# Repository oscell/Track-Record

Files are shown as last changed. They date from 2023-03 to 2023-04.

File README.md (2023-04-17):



## Team

| Name | Responsibility | GUID |
|---|---|---|
| Oscar Meunier | Network and Design engineer | 2391076M |
| Sai Vamsi Karnam | Development and Integration engineer | 2805927K |
| Tara Duggan | Electronics and Design engineer | 2363956D |
| Rohith Kambampati | Backend developer and programmer | 2782679K |

Track-Record is a face tracking system built on the Raspberry Pi 3B platform, using a Pi Camera Module and servo motors for real-time face detection and tracking. A GUI is also implemented which communicates via a server sending commands to the Raspberry Pi.

The full documentation can be found [here](https://tduggan63.github.io/Track-Record/index.html).

Find us on [Twitter](https://twitter.com/TrackrecordTeam) and [Instagram](https://www.instagram.com/_u/tracknrecordteam) to stay up to date with any of the latest developements or email us at tracknrecordteam@gmail.com to get in touch.

## Hardware

The following electronic components were used to build the project:

- [Raspberry Pi 3B](https://www.raspberrypi.com/products/raspberry-pi-3-model-b/)

- [SD Card] - One with a memory capacity of 16 gigs or more.
- [Pi Camera module 2](https://www.raspberrypi.com/products/camera-module-v2/)
- [SG92R Servo](https://www.towerpro.com.tw/product/sg92r-7/)

## Software Dependencies

The following libraries were used throughout the project:

- [CMake](https://cmake.org/download/)
- [OpenCV](https://opencv.org/releases/)
- [BCM2835](https://www.airspayce.com/mikem/bcm2835/index.html)
- [QT5](https://wiki.qt.io/Qt_for_Beginners)

## Installation and Usage

This project aims to build a standalone plug and play type product.
Clip the camera of your choice to the platform, switch the power on and watch it track you.
But wait there's more, you can build it on your own. Follow the instructions ahead.

## Instructions

- Step 1: Setting up the hardware
  - [Install the OS](https://www.raspberrypi.com/documentation/computers/getting-started.html) and set up a display.*
  - [Connect the Pi camera](https://www.raspberrypi.com/documentation/computers/compute-module.html#attaching-a-raspberry-pi-camera-module)
  - Connect the motors using the PinOut diagram: Pan at Gpio 18, Tilt at Gpio 17
  - 3D print the models -- Check the Schematics and Solidworks directories or build your own model

- Step 2: Software
  - Make sure to have the latest update for the GCC/G++ compiler on your Raspberry Pi OS.
  - [Setup cmake](https://cmake.org/download/) on your Raspberry Pi.
  - Clone the repo, the libraries used are included with the git package.
  
  ```git
  git clone https://github.com/oscell/Track-Record.git
  ```
  
  - Unpack the lib_package archive to /usr/include

  ```bash
  sudo tar -xf lib_package.tar.gz -C /usr/include
  ```
  
  - Create an executable in the `main/build` directory
    - Open a terminal and navigate to the main directory
    - Run the following commands to create the executable "tracknrecord"
  
    ```bash
    mkdir -p build && cd build
    cmake ..
    make
    ```

    - You should now see two executables named "tracknrecord" and "server" in the directory
  
  - Set executable permission to run on startup
    - Open a terminal and run the following commands
  
    ```bash
    mkdir /home/pi/.config/autostart
    nano /home/pi/.config/autostart/track.desktop
    ```

    - Copy or type the following text into the "track.desktop" file.
    - Replace the "directory" with the location of the executable named 'server.cpp' located in the main folder. (eg. home/pi/...)

    ```bash
    [Desktop Entry]
    Type=Application
    Name=Track
    Exec="directory"
    ```

    - Save the file using: Ctrl+X -> Y
  
- Step 3:
  - Setup the GUI* as shown in section 2 of the footnotes.

- Step 4:
  - Reboot the Pi from the terminal and it is ready to go.

    ```bash
    sudo reboot
    ```

  - The Pi should now be listening for commands.

  - Ensure the Pi and your personal machine are on the same network.

  - Open the GUI on your personal machine and click "start tracking".

  - To view the video feed, click the video feed button.

-----------------------------------------------------------------------------------------------------------------------------------------------------------------------

## *Footnotes  
  
### Section 1: Additonal information

- [Raspberry Pi PinOut diagram](https://www.raspberrypi.com/documentation/computers/raspberry-pi.html)
- SG92r wiring: Red for Power, Brown for Ground, and Yellow/Orange for Data.
- Set up [Raspberry Pi in headless mode](https://www.realvnc.com/en/blog/how-to-setup-vnc-connect-raspberry-pi/) without a display and other hardware.

### Section 2: GUI

This section should be built locally (not on the raspberry PI). It will be used to comunicate with the PI to send commands.

#### Dependencies

As previously with the raspi install [cmake](https://cmake.org/download/) on your machine. The next step is to install [Qt5](https://www.qt.io/download) although this can be done simply on linux using the command:

```bash
sudo apt-get install qt5-default
```

To find the path of your Qt5 installation, set up the C++, cmake, and QT5 on your personal machine and run the following command in the terminal:

```bash
find / -iname Qt5Config.cmake 2>/dev/null
```

Once you have the path, you can update the `/local/CMakeLists.txt` file with the correct Qt5_DIR.

```cmake
set(Qt5_DIR "/path/to/Qt5/lib/cmake/Qt5")
```

The comunication with the raspberry pi is done through a server. To find the IP adress of the raspery pi run in the raspberry pi terminal:

```bash
hostname -I
```

In `/local/src/GUI/main.cpp` change:

```c++
QString serverAddress = "127.0.0.1";
```

to

```c++
QString serverAddress = "<raspberry_pi_ip>"
```

### Build

```bash
cd local/
mkdir -p build && cd build
cmake ..
make
```

### Usage

### On the Raspi

Before being able to run send command the server must be initialised on the raspi.

```bash
cd main/build/
./server 
```

### On your local machine

Run the GUI.

```bash
 cd local/build/
./GUI1_0
```

It is comprised of a section for vieo feed input and 2 buttons.

### Tracking button

This sends a signal to the client which toggles the tracknrecord executable depending on the state it is currently in.

### Video feed

This toggles the user webcam to show how face detection and tracking works.
The GUI should look like this:

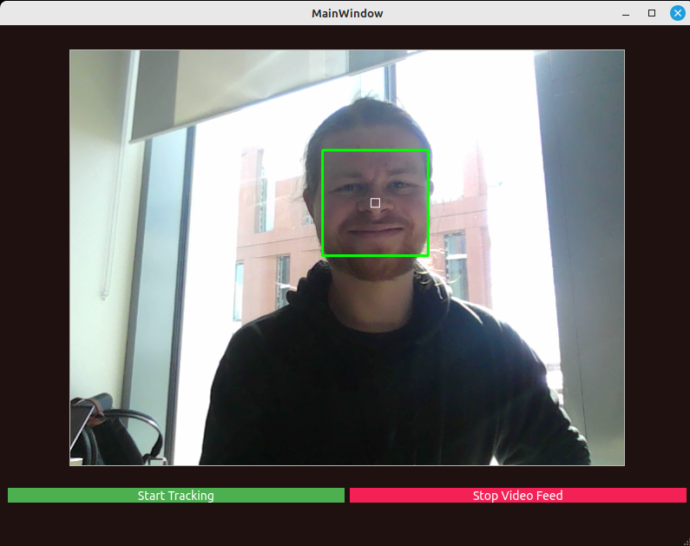
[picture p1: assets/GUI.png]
GUI


### Section 3: Testing

The test report and the code we used for tests is available on a different branch of this repo. It can be accessed using https://github.com/oscell/Track-Record/tree/tests/tests

### Section 4: 3D printing material

The Solidworks assemblies are provided in `Solidworks/`. This will require version 2022 or above however. To print the latest version of the stand `.stl` files are available in `Solidworks/Stls/`.

### Exploded view

***Note***: In out product demonstration the base used was the `Base_old` as we did not have time to 3D print such a large base.

Once assembled model looks like:

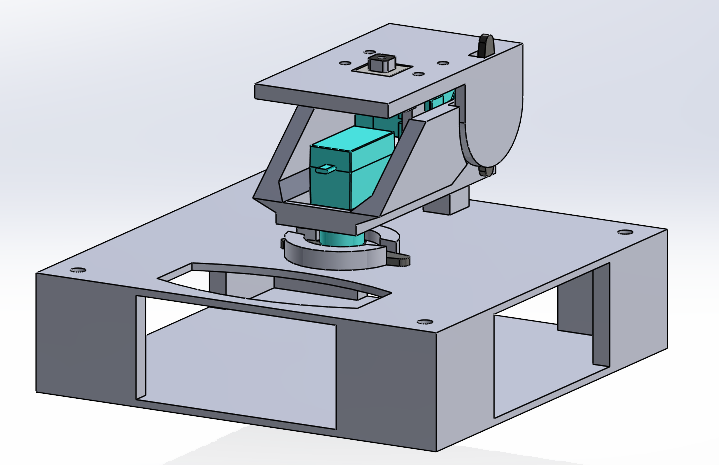
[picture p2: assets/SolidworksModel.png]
NormalVew


and in exploded view:

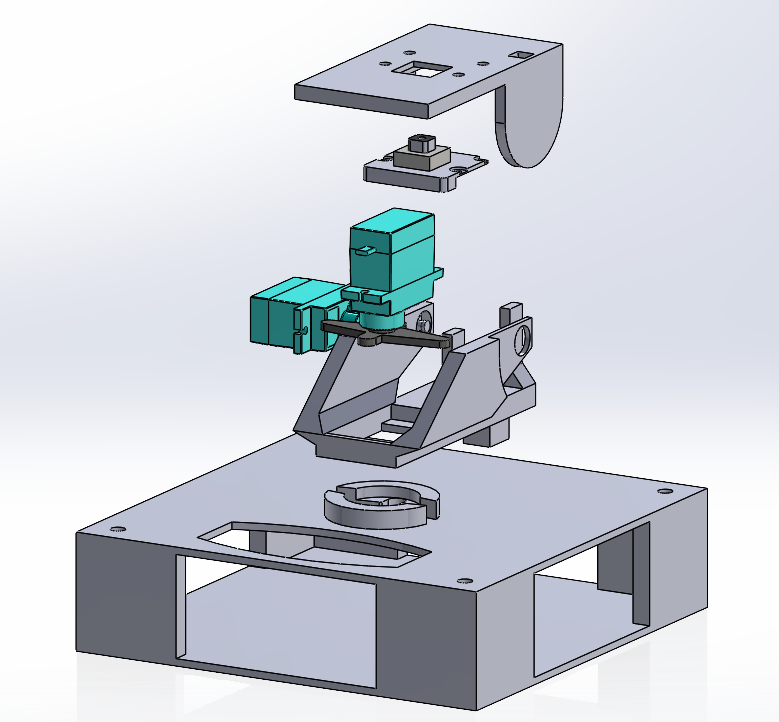
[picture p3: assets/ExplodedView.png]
explodeView


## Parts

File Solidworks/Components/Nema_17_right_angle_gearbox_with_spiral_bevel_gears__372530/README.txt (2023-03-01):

Nema 17 right angle gearbox with spiral bevel gears  by dasaki on Thingiverse: https://www.thingiverse.com/thing:372530

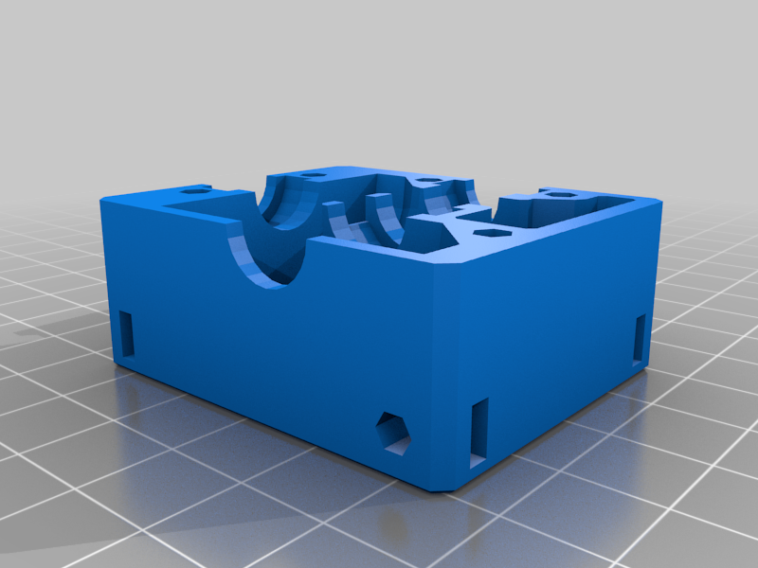
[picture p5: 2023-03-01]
Solidworks/Components/Nema_17_right_angle_gearbox_with_spiral_bevel_gears__372530/images/enclosure_side_B_open.png

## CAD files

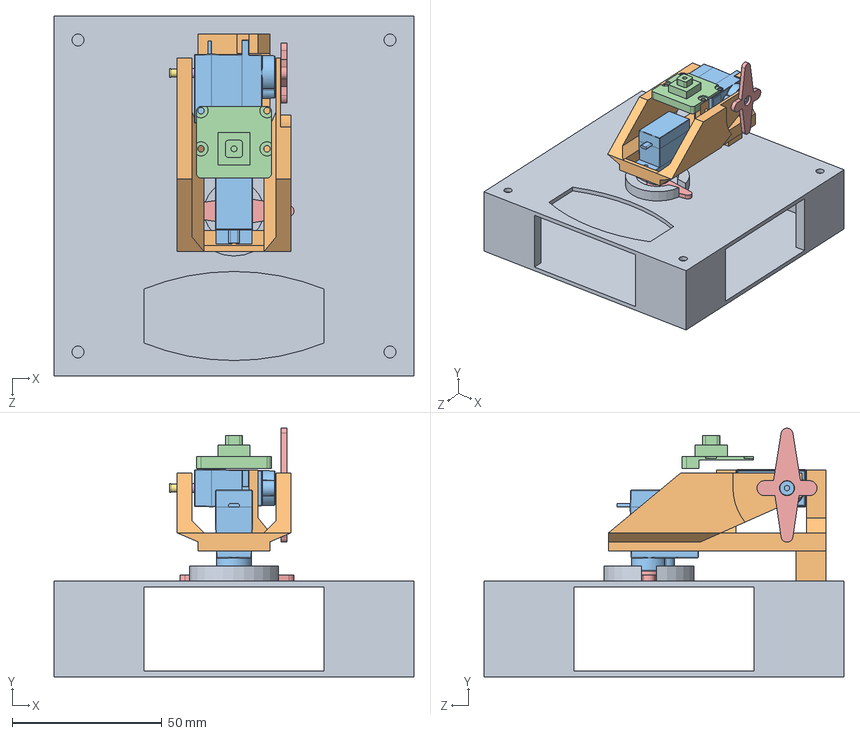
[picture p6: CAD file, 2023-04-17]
Solidworks/2DofStandv2.SLDASM
120.0 x 82.9 x 120.0 mm
Base
Panmount
TowerPro SG92R Servo Motor x 2
CameraModule3
hub x 2
Pin_inner
Pin_outer

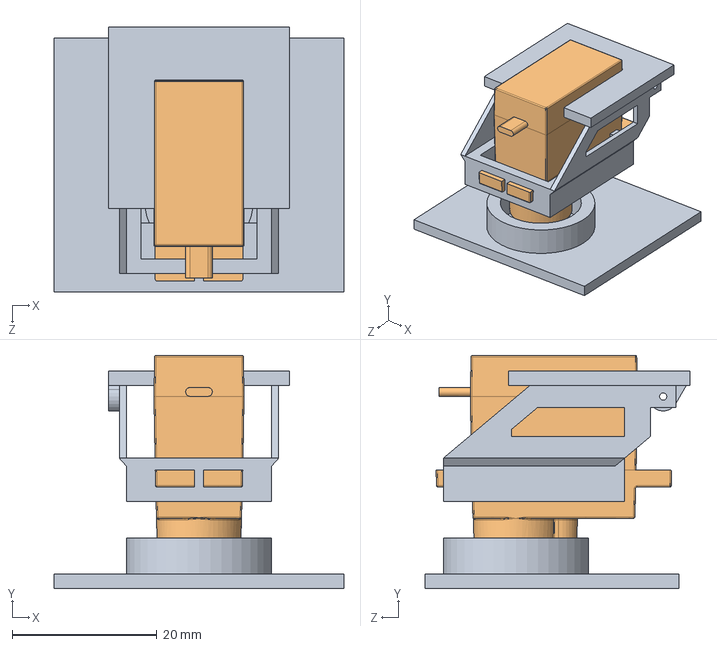
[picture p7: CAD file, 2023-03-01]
Solidworks/TestingAssemblies/Assem1.SLDASM
40.0 x 32.2 x 36.5 mm
2DofStandv2
TowerPro SG92R Servo Motor

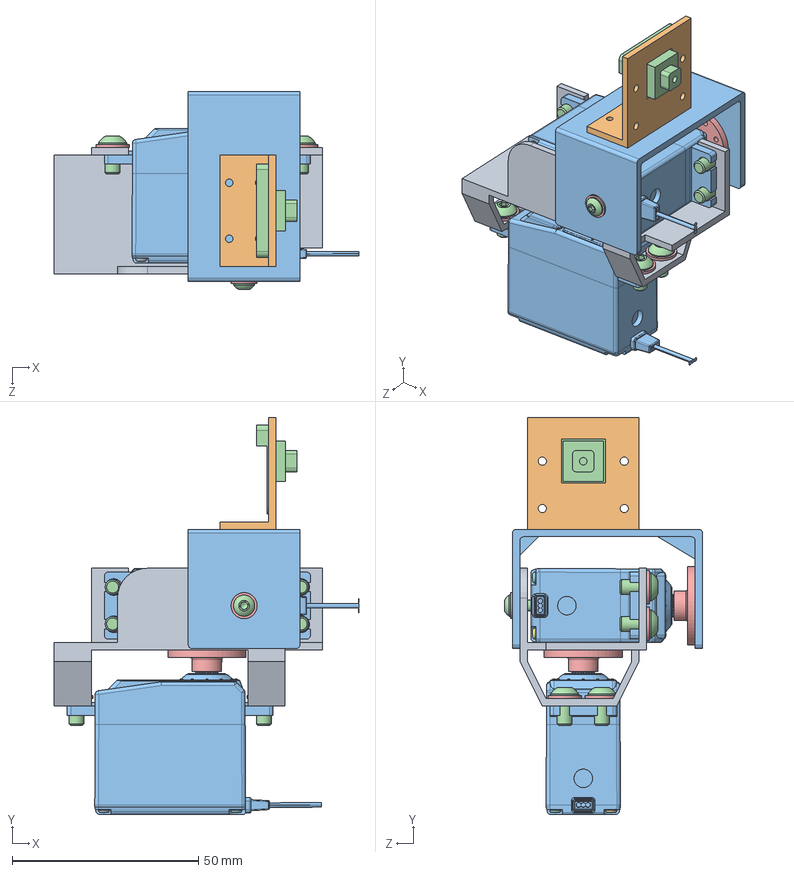
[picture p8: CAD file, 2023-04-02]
Solidworks/2DofStand.SLDASM
81.8 x 106.5 x 53.2 mm
Bracket(bottom)
CameraMount
Bracket(top)
CameraModule3
HORN-D x 2
Screw_3x8 x 2
b4 x 2
b3 x 2
b2 x 2
b1 x 2
Case x 2
socket button head screw_iso x 9
plain washer normal grade a_iso x 9

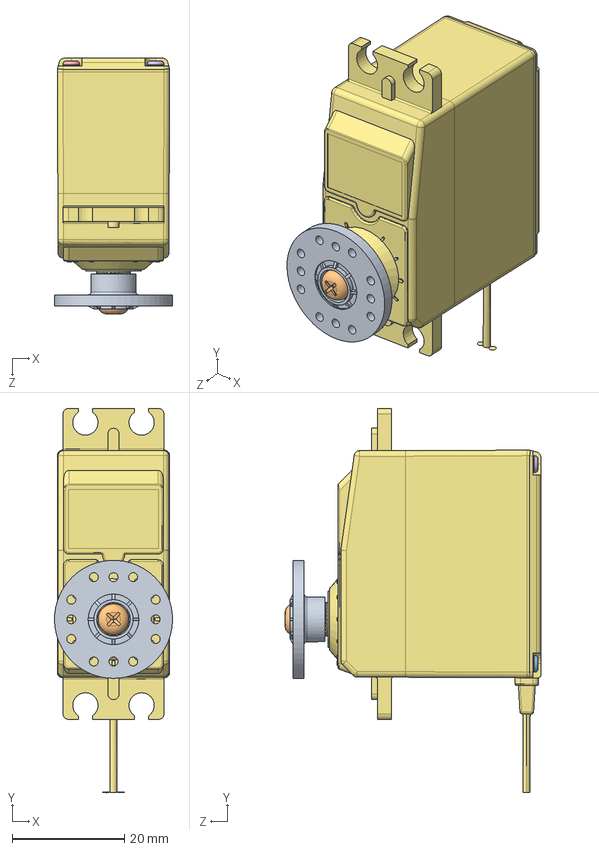
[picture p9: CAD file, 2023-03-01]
Solidworks/Components/Parallax-900-00005-08-25-Servo-CR-HSCR-STD.SLDASM
21.0 x 68.3 x 45.5 mm
HORN-D
Screw_3x8
b4
b3
b2
b1
Case

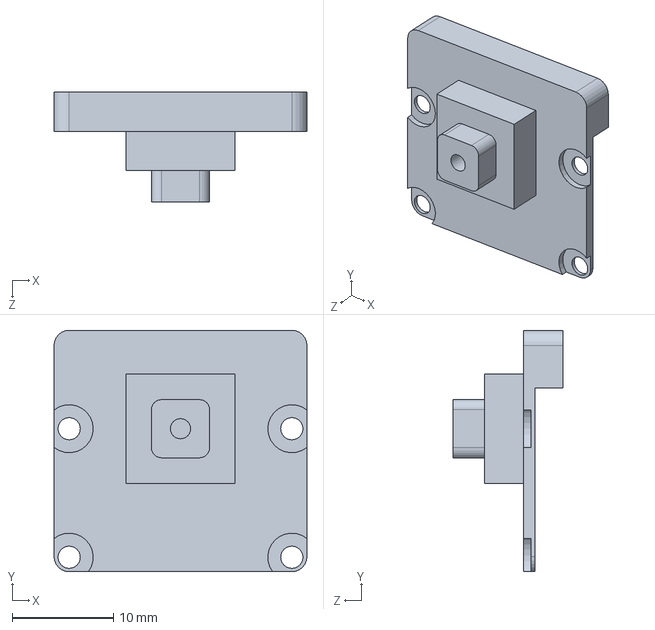
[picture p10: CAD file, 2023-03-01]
Solidworks/Components/Cameras/CameraModule3.SLDPRT
25.0 x 23.9 x 10.9 mm

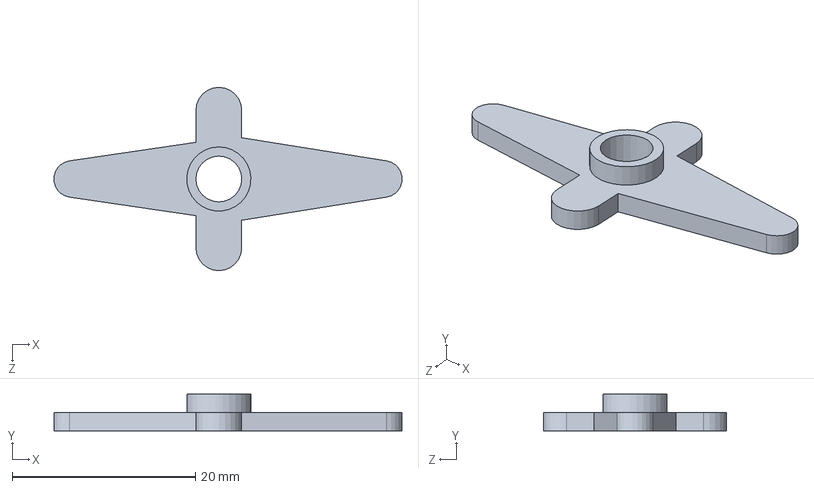
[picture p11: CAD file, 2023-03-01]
Solidworks/Components/Motors/tower-pro-sg92r-servo-motor-1.snapshot.5/hub.SLDPRT
38.0 x 4.00 x 20.0 mm

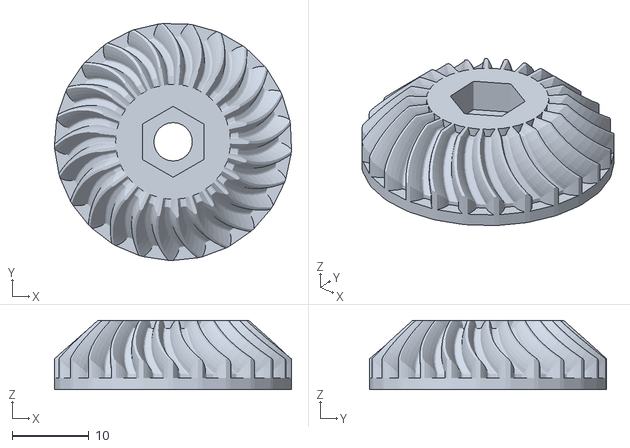
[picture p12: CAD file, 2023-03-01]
Solidworks/Components/Nema_17_right_angle_gearbox_with_spiral_bevel_gears__372530/files/spiral_bevel_gear_R.stl
30.9 x 30.8 x 9.00

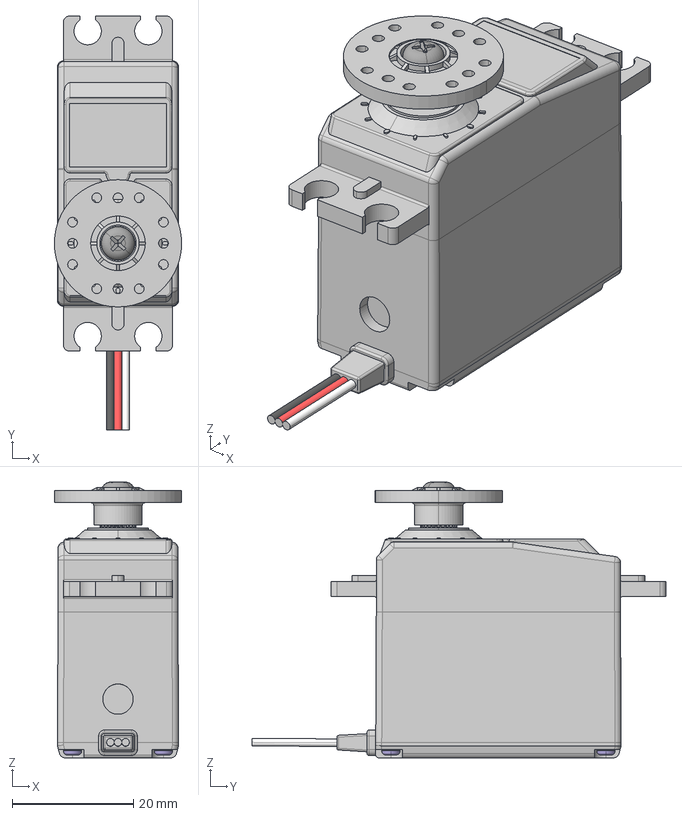
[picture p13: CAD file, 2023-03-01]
Solidworks/MechanicalDrawings/Parallax-900-00005-08-25-Servo-CR-HSCR-STD/Parallax-900-00005-08-25-Servo-CR-HSCR-STD.stp
21.0 x 68.3 x 45.5 mm
HORN-D
Screw_3x8
b4
b3
b2
b1
Case

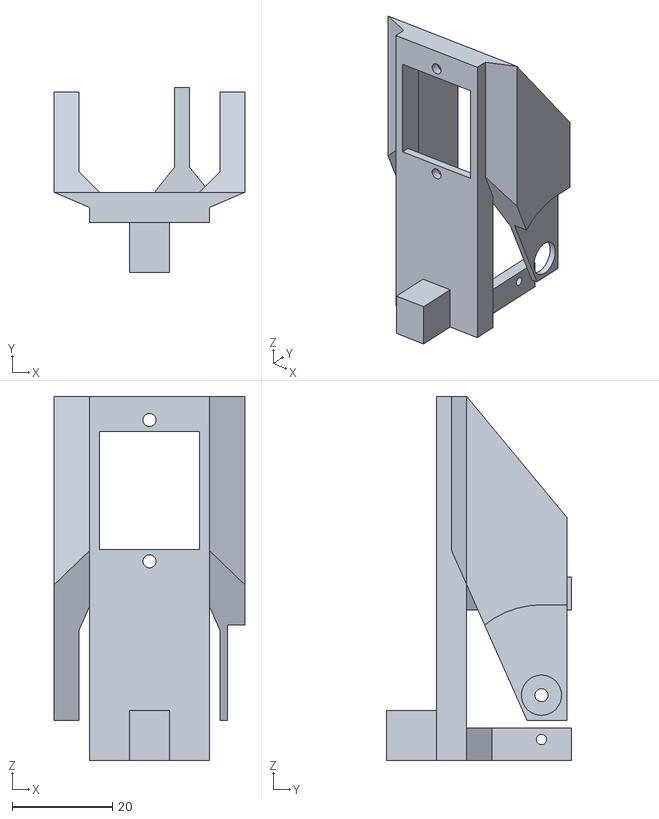
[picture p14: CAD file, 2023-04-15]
Solidworks/Stls/2DofStandv2 - Panmount-1.STL
38.0 x 36.9 x 72.5

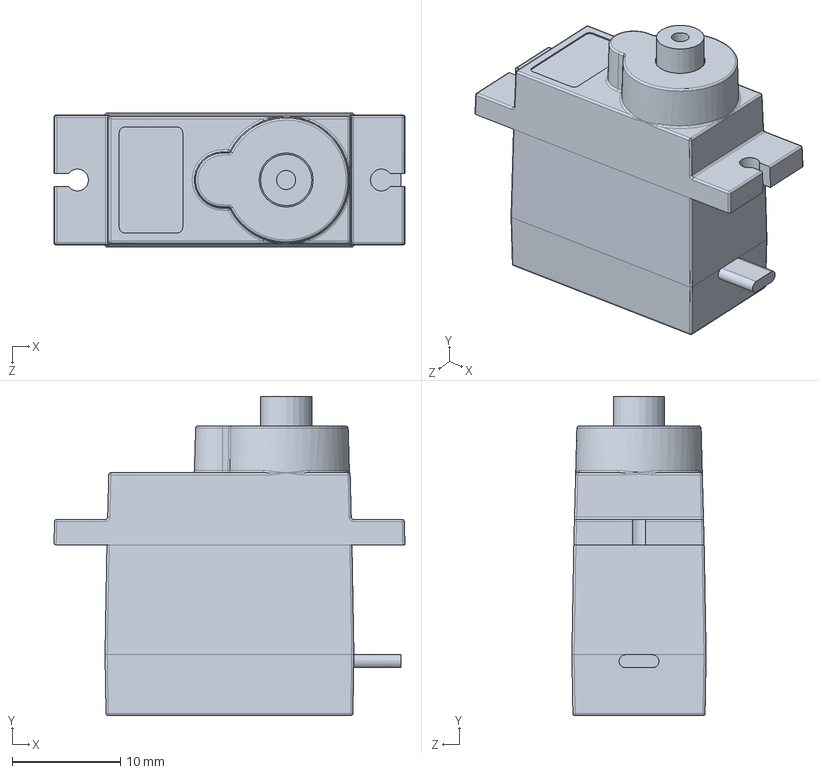
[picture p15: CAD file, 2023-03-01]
Solidworks/Components/Motors/tower-pro-sg92r-servo-motor-1.snapshot.5/TowerPro SG92R Servo Motor.SLDPRT
32.5 x 29.6 x 12.4 mm

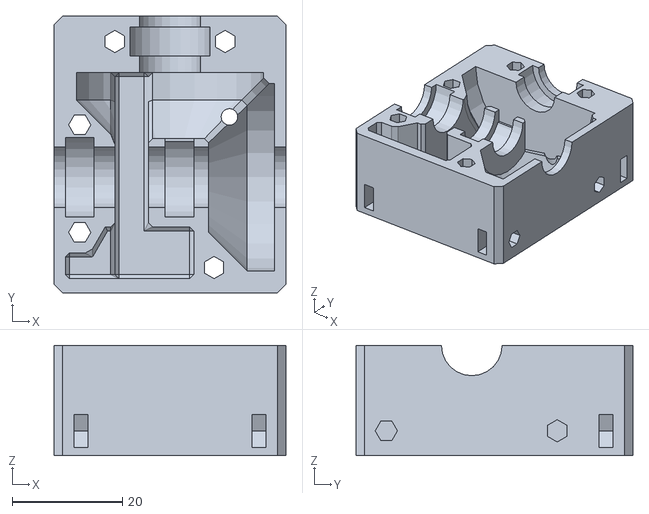
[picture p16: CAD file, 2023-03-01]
Solidworks/Components/Nema_17_right_angle_gearbox_with_spiral_bevel_gears__372530/files/enclosure_side_A.stl
42.0 x 50.3 x 20.0

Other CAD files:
Solidworks/Components/HORN-D.SLDPRT
Solidworks/Parts/Standv1/CameraMount.SLDPRT
Solidworks/Parts/Standv2/Pin_outer.SLDPRT
Solidworks/Parts/Standv1/MotorHub(bottom).SLDPRT
Solidworks/Parts/Standv2/Pin_inner.SLDPRT
Solidworks/Components/b3.SLDPRT
Solidworks/Components/Nema_17_right_angle_gearbox_with_spiral_bevel_gears__372530/files/enclosure_side_A_open.stl
Solidworks/2DofStand.SLDPRT
Solidworks/2DofStandv2.SLDPRT
Solidworks/Components/Case.SLDPRT
Solidworks/Components/Nema_17_right_angle_gearbox_with_spiral_bevel_gears__372530/files/enclosure_side_B.stl
Solidworks/Components/Nema_17_right_angle_gearbox_with_spiral_bevel_gears__372530/files/enclosure_side_B_open.stl
Solidworks/Components/Nema_17_right_angle_gearbox_with_spiral_bevel_gears__372530/files/nema_17_right_angle_gearbox.skp
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

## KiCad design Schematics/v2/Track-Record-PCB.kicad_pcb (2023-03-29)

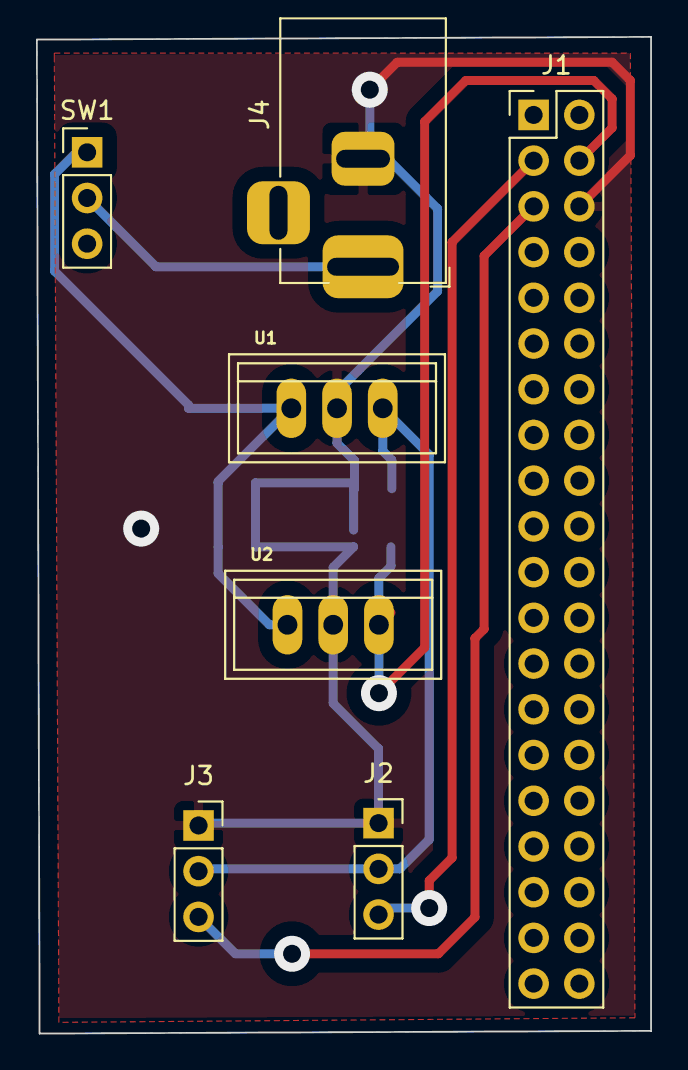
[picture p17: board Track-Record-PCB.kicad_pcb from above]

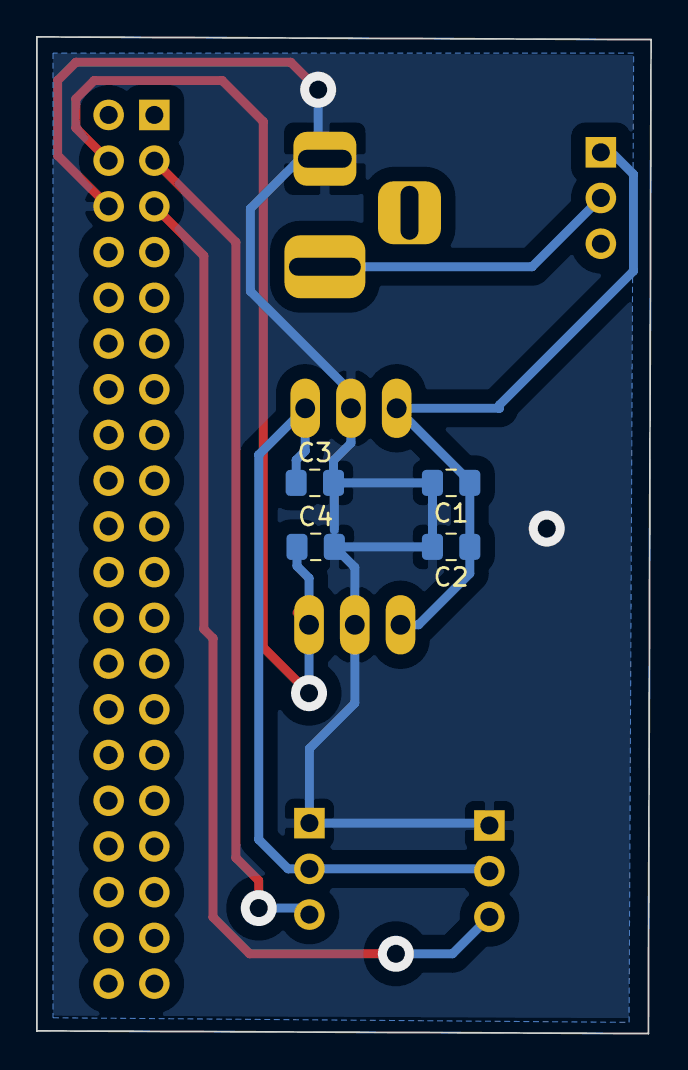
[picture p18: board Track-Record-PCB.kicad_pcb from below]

Board: 2 copper layers, 34.1 x 55.4 mm, 11 parts (4 on the bottom side), 7 nets.

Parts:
C1, C2: 0.33u; C_0805_2012Metric_Pad1.18x1.45mm_HandSolder
C3, C4: 0.1u; C_0805_2012Metric_Pad1.18x1.45mm_HandSolder
J1: RPI3_Connector; PinSocket_2x20_P2.54mm_Vertical
J2: Motor_1; PinSocket_1x03_P2.54mm_Vertical
J3: Motor_2; PinSocket_1x03_P2.54mm_Vertical
J4: 12V_connector; BarrelJack_Horizontal
SW1: Power Switch; PinHeader_1x03_P2.54mm_Vertical
U1, U2: L7805; TO-220-STANDING

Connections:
+5V: C3.1, J2.2, J3.2, U1.3
+5VD: C4.1, J1.4, U2.3
+12V: J4.1, SW1.2
+12VA: C1.1, C2.1, SW1.1, U1.1, U2.1
/Signal_1: J1.3, J2.3
/Signal_2: J1.5, J3.3
GND: C1.2, C2.2, C3.2, C4.2, J1.6, J2.1, J3.1, J4.2, U1.2, U2.2

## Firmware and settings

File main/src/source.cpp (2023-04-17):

#include <iostream>
#include <vector>
#include <string.h>
#include <stdlib.h>
#include <ctype.h>
#include <bcm2835.h>
#include <opencv2/opencv.hpp>
#include <opencv2/highgui.hpp>
#include <opencv2/imgproc.hpp>
#include <opencv2/core/ocl.hpp>


/**
 * @class movement
 * @brief Class to control pan-tilt camera movement using Raspberry Pi GPIO
 * This class provides functions to move the pan and tilt motors of a camera connected to
 * Raspberry Pi using the bcm2835 library to control the GPIO pins. The class also includes
 * variables to calculate the pulse and on-time required to send signals to the motors.
 *
 */
class movement 
{
	private:
    	float pulse; /**< Pulse required to move the motor in degrees. Float because pulse for 3 degree angle is too small for an integer typecast */
	int i; /**< Counter variable */
	int angle;
	float on_time = 10.3*angle+546; /**< On-time required to send signal to the motor */

	public:
	/**
         * @brief Function to move the pan motor
         *
         * This function takes the desired angle, previous angle, and alignment information
         * as input and calculates the pulse required to move the motor. It then sends signals
         * to the motor using the bcm2835 library to move it to the desired angle.
         *
         * @param angle Desired angle of the motor
         * @param prev_angle Previous angle of the motor
         * @param align Alignment information (0 or 1)
         */
	void pan(int angle, int prev_angle, int align) // Function for moving the pan motor connected at pin 18 
	{
		if (align==1)
		{
			pulse = 40; // It takes around 40 pulses to get 180 degree rotation
		}
		else
		{
			pulse = (float)abs(((angle-prev_angle)*40.0)/180.0); // Calculating the pulse required
		}
	
		// Controlling the motor according to the pulse calculated above
		for(i=0;i<pulse;i++)
		{
			bcm2835_gpio_set(18); // setting pin 18 to high
			bcm2835_delayMicroseconds((int)on_time); // leaving it on high for time specified
			bcm2835_gpio_clr(18); // setting pin 18 to low
		}
	}

	public:
	/**
    	* @brief Function to move the tilt motor
    	*
    	* This function takes the desired angle, previous angle, and alignment information
    	* as input and calculates the pulse required to move the motor. It then sends signals
    	* to the motor using the bcm2835 library to move it to the desired angle.
    	*
    	* @param angle Desired angle of the motor
    	* @param prev_angle Previous angle of the motor
    	* @param align Alignment information (0 or 1)
    	*/
	void tilt(int angle, int prev_angle, int align) // Function for moving the tilt motor connected at pin 17
	{	
		if (align==1)
		{
			pulse = 40; // It takes around 40 pulses to get 180 degree rotation
		}
		else
		{
			pulse = (float)abs(((angle-prev_angle)*40.0)/180.0); // Calculating pulse required
		}
	
		// Controlling the motor according to the pulse calculated above
		for(i=0;i<pulse;i++)
		{
			bcm2835_gpio_set(17); // setting pin 17 to high
			bcm2835_delayMicroseconds((int)on_time); // leaving it on high for time specified. Necessary to allow motor to move to required angle. 
			bcm2835_gpio_clr(17); // setting pin 18 to low
		}
	}
};

/**
 * @class recognition
 * @brief This class inherits from the movement class and contains functions for face tracking and detection.
 */
class recognition : public movement
{
	private:
	int increment = 3; /**< Increment to be added in pan/tilt angles */
	int start_angle = 90; /**< Starting angle of the motor */
	int pan_angle = 90; /**< Pan angle of the motor */
	int tilt_angle = 90; /**< Tilt angle of the motor */
	int flag  = 0; /**< Iterator */
	int prev_pan_angle = 0;  /**< Previous pan angle of the motor */
	int prev_tilt_angle = 0; /**< Previous tilt angle of the motor */
	
	public:
	std::vector<int> previous_angles; /**< Vector storing the previous pan and tilt angles */
    	/**
     	* @brief This function tracks the face based on conditions.
     	* @param x_face_centr X-coordinate of the face centroid
     	* @param y_face_centr Y-coordinate of the face centroid
     	* @param x_frame_centr X-coordinate of the frame centroid
     	* @param y_frame_centr Y-coordinate of the frame centroid
     	* @param itr Iterator
     	* @param prev_pan_angle Previous pan angle of the motor
     	* @param prev_tilt_angle Previous tilt angle of the motor
     	* @return A vector containing previous pan and tilt angles.
     	*/
	// Tracking the face based on conditions
	std::vector<int> track(int x_face_centr, int y_face_centr, int x_frame_centr, int y_frame_centr, int flag, int prev_pan_angle, int prev_tilt_angle)
	{
		if (x_face_centr > x_frame_centr+20)
		{
			pan_angle += increment;
			if (pan_angle > 180) // Limiting the angle increment to support motor hardware limitations
			{
				pan_angle = 180;
			}
			if (flag==1)
			{
				pan(pan_angle, start_angle, 0);
			}
			else
			{
				pan(pan_angle, prev_pan_angle, 0);
			}
			prev_pan_angle = pan_angle;
		}
		if (x_face_centr < x_frame_centr-20)
		{
			pan_angle -= increment;
			if (pan_angle < 0)  // Limiting the angle increment to support motor hardware limitations
			{
				pan_angle = 0;
			}			
			if (flag==1)
			{
				pan(pan_angle, start_angle, 0);
			}
			else
			{
				pan(pan_angle, prev_pan_angle, 0);
			}
			prev_pan_angle = pan_angle;
		}
		if (y_face_centr > y_frame_centr+20)
		{
			tilt_angle += increment;
			if (tilt_angle > 180) // Limiting the angle increment to support motor hardware limitations
			{
				tilt_angle = 180;
			}
			if (flag==1)
			{
				tilt(tilt_angle, start_angle, 0);
			}
			else
			{
				tilt(tilt_angle, prev_tilt_angle, 0);
			}
			prev_tilt_angle = tilt_angle;
		}
		if (y_face_centr < y_frame_centr-20)
		{
			tilt_angle -= increment;
			if (tilt_angle < 0) // Limiting the angle increment to support motor hardware limitations
			{
				tilt_angle = 0;
			}			
			if (flag==1)
			{
				tilt(tilt_angle, start_angle, 0);
			}
			else
			{
				tilt(tilt_angle, prev_tilt_angle, 0);
			}
			prev_tilt_angle = tilt_angle;
		}
		
	std::vector<int> previous_angles = {prev_pan_angle, prev_tilt_angle};
	return previous_angles;
}
    	/**
     	* @brief This function tracks the movement and orientation of the face in real-time using a webcam.
     	* This function initializes the webcam, loads the face detection model, captures frames from the webcam,
     	* detects faces in the captured frames, and tracks the movement and orientation of the detected faces.
     	* @return 0 if the tracking was successful, -1 if there was an error.
     	*/
	int vision()
	{
		previous_angles = {prev_pan_angle, prev_tilt_angle};
	
		// Initialsing the webcam
		ocl::setUseOpenCL(false); // Disabling OpenCL to reduce frame lag due to GPU dependencies
		cv::VideoCapture cap(0); // 0 is default camera (when only one is connected), 1 is usb webcam when both are connected
		cap.set(CAP_PROP_FRAME_WIDTH, 1280);
		cap.set(CAP_PROP_FRAME_HEIGHT, 720);
	
		// Opening videocapture class
		if (!cap.isOpened()) 
		{
			std::cerr << "Error opening the camera, check initialisation, connection, and hardware" << std::endl;
			return -1;
		}
	
		// Loading the face detection model
		cv::CascadeClassifier face_det;
		if(!face_det.load("/usr/include/opencv/data/haarcascades/haarcascade_frontalface_default.xml"))
		{
			std::cerr << "Error loading the model, check opencv installation and the cascade libraries" << std::endl;
			return -1;
		}
	
		cv::Mat frame;
		cv::Mat gray;
		
		// Processing the frames to get required values
		while (cap.read(frame))
		{
			// Getting the center co-ordinates of the captured frame
			int x_frame_centr = (frame.cols*0.5); // Cap width div by 2
			int y_frame_centr = (frame.rows*0.5); // Cap height div by 
			
			cv::cvtColor(frame, gray, cv::COLOR_BGR2GRAY); // Converting the frames to grayscale to enable better face detection
			cv::flip(gray, gray, 1); // Flipping the frame horizontally

			// Detecting the faces from the grayscale frames and storing them in "faces" 
			std::vector<cv::Rect> faces;
			face_det.detectMultiScale(gray, faces, 1.5, 6, CV_HAAR_DO_CANNY_PRUNING, Size(30,30)); // Change the parameters for debugging
		
			for (const auto& face : faces)
			{
				// Getting the center co-ordinates of the detected face
				int x_face_centr = (face.x + face.width * 0.5);
				int y_face_centr = (face.y + face.height * 0.5);
			
				flag += 1;
				// Tracking the face using center values
				previous_angles = track(x_face_centr, y_face_centr, x_frame_centr, y_frame_centr, flag, previous_angles[0], previous_angles[1]); // Calling the track function
			}
		
			// Debugging for development -- Show the captured frames (Video Feed)
			/*
			// Show the frame in grayscale for better speed
			cv::imshow("Webcam Feed", gray);   
		
			// Exit the loop if the user presses 'q'
			if (cv::waitKey(1) == 'q')
			{
				break;
			}
			*/
		}	
		// Returning 0 so that control does not reach end of non-void function
		return 0;			
	}
};

/**
* @brief Main function to run motor and vision control
* This function initializes the BCM2835 library and connects to the motor.
* It sets pin 17 and pin 18 as output for motor control.
* Then it sets the Pan motor and Tilt motor at 90 degrees as the starting pose
* by calling the respective functions of the recognition object.
* Finally, it calls the vision function of the recognition object.
* @return 0 on success
*/
int main()
{
	recognition obj;
	{
		// Initialising BCM2835 to connect to the motor
		if(!bcm2835_init())
		{
			std::cout << ("motor not initialised") << std::endl;
		}
		
		// Connecting pin 17 and pin 18 as output
		bcm2835_gpio_fsel(18, BCM2835_GPIO_FSEL_OUTP);
		bcm2835_gpio_fsel(17, BCM2835_GPIO_FSEL_OUTP);
		
		// Setting Pan motor at 90 degrees as the starting pose
		obj.pan(90, 0, 1);
		
		// Setting Tilt motor at 90 degrees as the starting pose
		obj.tilt(90, 0, 1);
		
		// Calling vision function
		obj.vision();
	}
    
    // Returning 0 so that control does not reach end of non-void function
    return 0;
}

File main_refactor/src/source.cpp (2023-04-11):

#include <iostream>
#include <vector>
#include <string.h>
#include <stdlib.h>
#include <ctype.h>
#include <bcm2835.h>
#include <opencv2/opencv.hpp>
#include <opencv2/highgui.hpp>
#include <opencv2/imgproc.hpp>
#include <opencv2/core/ocl.hpp>

// Global variables
int increment = 3; // Angle increment: higher value makes motor move fast but causes jitter, fine tune according to model stability 
int start_angle = 90;
int pan_angle = 90;
int tilt_angle = 90;


// Function for moving the pan motor connected at pin 18 
void pan(int angle, int prev_angle, int align) 
{
	float pulse;
	int i;
	float on_time = 10.3*angle+546; // calculating on time for sending data to motor
	
	if (align==1)
	{
		pulse = 40; // It takes around 40 pulses to get 180 degree rotation
	}
	else
	{
		pulse = (float)abs(((angle-prev_angle)*40.0)/180.0); // calculating pulse for change in angle (PWM)
	}
	
	// Controlling the motor according to the pulse calculated above
	for(i=0;i<pulse;i++)
	{
		bcm2835_gpio_set(18); // setting pin 18 to high
		bcm2835_delayMicroseconds((int)on_time); // leaving it on high for time specified
		bcm2835_gpio_clr(18); // setting pin 18 to low
		bcm2835_delayMicroseconds(20000 - (int)on_time); // 20000 = 20ms
	}
}


// Function for moving the tilt motor connected at pin 17
void tilt(int angle, int prev_angle, int align) 
{
	float pulse; // float because pulse for 3 degree angle is too small for an integer typecast
	int i;
	float on_time = 10.3*angle+546; // previous: 10.3*angle+340, default = 546
	

	if (align==1)
	{
		pulse = 40; // It takes around 40 pulses to get 180 degree rotation
	}
	else
	{
		pulse = (float)abs(((angle-prev_angle)*40.0)/180.0); // calculating pulse for change in angle (PWM)
	}
	
	// Controlling the motor according to the pulse calculated
	for(i=0;i<pulse;i++)
	{
		bcm2835_gpio_set(17); // setting pin 17 to high
		bcm2835_delayMicroseconds((int)on_time); // leaving it on high for time specified
		bcm2835_gpio_clr(17); // setting pin 18 to low
		bcm2835_delayMicroseconds(20000 - (int)on_time); // 20000 = 20ms
	}
}


// Function for conditional tracking
vector<int> track(int x_face_centr, int y_face_centr, int x_frame_centr, int y_frame_centr, int itr, int prev_pan_angle, int prev_tilt_angle)
{
		
	if (itr == 1)
	{
		if (x_face_centr > x_frame_centr+20)
		{
			pan_angle += increment;
			if (pan_angle > 180)
			{
				pan_angle = 180;
			}
			pan(pan_angle, start_angle, 0);
			prev_pan_angle = pan_angle;
		}
		if (x_face_centr < x_frame_centr-20)
		{
			pan_angle -= increment;
			if (pan_angle < 0)
			{
				pan_angle = 0;
			}			
			pan(pan_angle, start_angle, 0);
			prev_pan_angle = pan_angle;
		}
		if (y_face_centr > y_frame_centr+20)
		{
			tilt_angle += increment;
			if (tilt_angle > 180)
			{
				tilt_angle = 180;
			}
			tilt(tilt_angle, start_angle, 0);
			prev_tilt_angle = tilt_angle;
		}
		if (y_face_centr < y_frame_centr-20)
		{
			tilt_angle -= increment;
			if (tilt_angle < 0)
			{
				tilt_angle = 0;
			}			
			tilt(tilt_angle, start_angle, 0);
			prev_tilt_angle = tilt_angle;
		}
	}
	else
	{
		if (x_face_centr > x_frame_centr+20)
		{
			pan_angle += increment;
			if (pan_angle > 180)
			{
				pan_angle = 180;
			}
			pan(pan_angle, prev_pan_angle, 0);
			prev_pan_angle = pan_angle;
		}
		if (x_face_centr < x_frame_centr-20)
		{
			pan_angle -= increment;
			if (pan_angle < 0)
			{
				pan_angle = 0;
			}				
			pan(pan_angle, prev_pan_angle, 0);
			prev_pan_angle = pan_angle;
		}
		if (y_face_centr > y_frame_centr+20)
		{
			tilt_angle += increment; 
			if (tilt_angle > 180)
			{
				tilt_angle = 180;
			}
			tilt(tilt_angle, prev_tilt_angle, 0);
			prev_tilt_angle = tilt_angle;
		}
		if (y_face_centr < y_frame_centr-20)
		{
			tilt_angle -= increment;
			if (tilt_angle < 0)
			{
				tilt_angle = 0;
			}			
			tilt(tilt_angle, prev_tilt_angle, 0);
			prev_tilt_angle = tilt_angle;
		}	
	}
	vector<int> previous_angles = {prev_pan_angle, prev_tilt_angle};
	return previous_angles;
}
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

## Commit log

2023-03-01 Added Solidworks directory
    [2DofStand.SLDASM, 2DofStand.SLDPRT, 2DofStandv2 - Base-1.STL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]
2023-03-15 add schematics and PCB files
    [Track-Record-PCB.kicad_pcb, Track-Record-sch.sch]
2023-03-21 V3 Stls
    [2DofStandv2 - Base-1.STL, 2DofStandv2 - CameraModule3-1.STL, 2DofStandv2 - Panmount-1.STL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]
2023-03-25 Add files via upload
    PCB files for UofG manufacture
    [Track-Record-PCB.kicad_pcb, Track-Record-sch.sch]
2023-04-02 resvised solidworks designs
    [2DofStand.SLDASM, 2DofStandv2 - Base-1.STL, 2DofStandv2 - Panmount-1.STL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]
2023-04-11 Delete motor moving directory
    Removing redundant directories
2023-04-13 old STL
    [2DofStandv2 - Base-1.STL, 2DofStandv2 - Panmount-1.STL, 2DofStandv2 - TiltMount-1.STL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]
2023-04-15 added updated stls
    [2DofStandv2 - Base-1.STL, 2DofStandv2 - Panmount-1.STL, 2DofStandv2 - TiltMount-1.STL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]
2023-04-17 added a 3D printing material section
    [2DofStandv2.SLDASM]
